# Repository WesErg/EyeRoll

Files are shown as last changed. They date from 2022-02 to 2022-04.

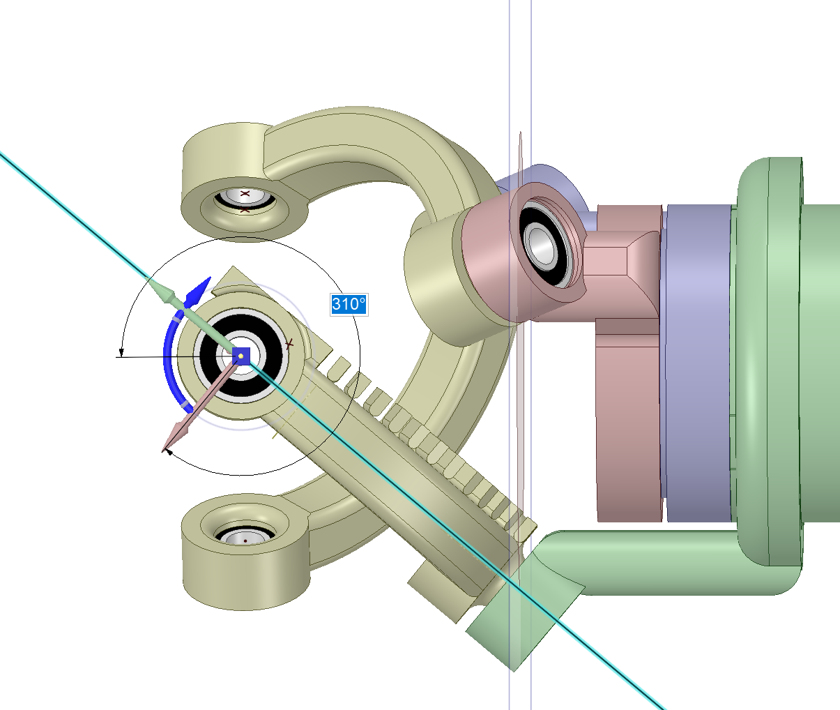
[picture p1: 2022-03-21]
doc/photos/Measure_joint_3_2_orientation.png

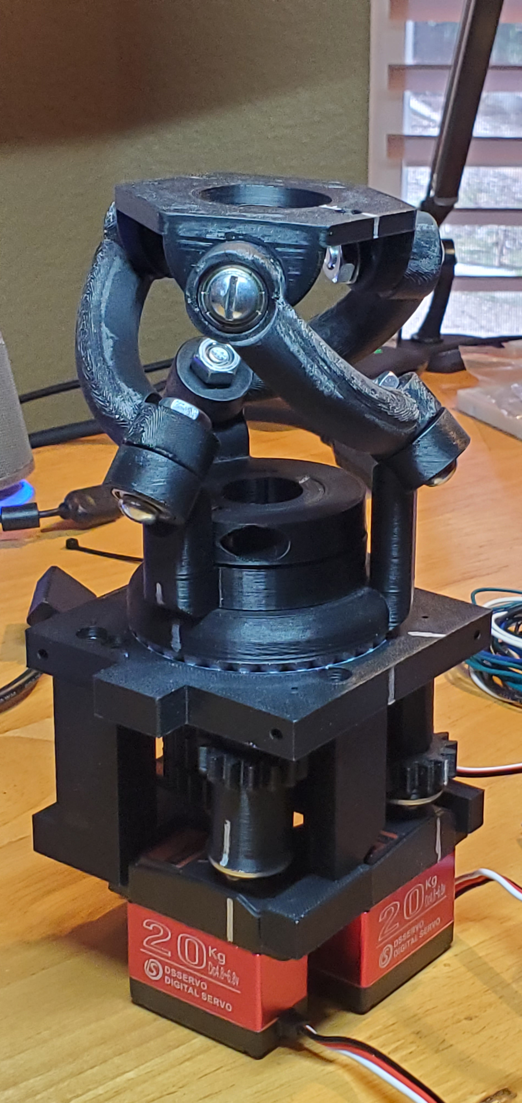
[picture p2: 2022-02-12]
doc/photos/wrist_assembled.jpg

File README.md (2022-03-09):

# EyeRoll
Project Eye Roll captures my explorations with a parallel spherical joint wrist (neck) as a means to produce a human eye roll.

A funny story ... never mind.

## References

[DruppThingaVerse](https://www.thingiverse.com/thing:2059967/files) Inmoov_New Neck by Drupp January 24, 2017.

[DruppInmoov](https://www.drupp.eu/inmoov.html) Drupp's inmoov page.

[Bulgarelli, et. al.](https://journals.sagepub.com/doi/pdf/10.5772/64113) A Low-cost Open Source 3D-Printable Dexterous Anthropomorphic Robotic Hand with a Parallel Spherical Joint Wrist for Sign Languages Reproduction.

[Sudki, Lauria, Nuca](https://www.marinepropulsors.com/proceedings/2013/10A.3.pdf) Marine Propulsor based on a Three-Degreee-of-Freedom Actuated Spherical Joint

[VideoServoTest](https://youtu.be/cDstRL1lU_U) video excercising joint

[Be Quiet](https://odriverobotics.com/#odrive)

## Project Manafest (fancy to do list right now)
- [ ] Jupyter notebook capturing the math
- [ ] Bill of Materials
- [ ] Python joint driver

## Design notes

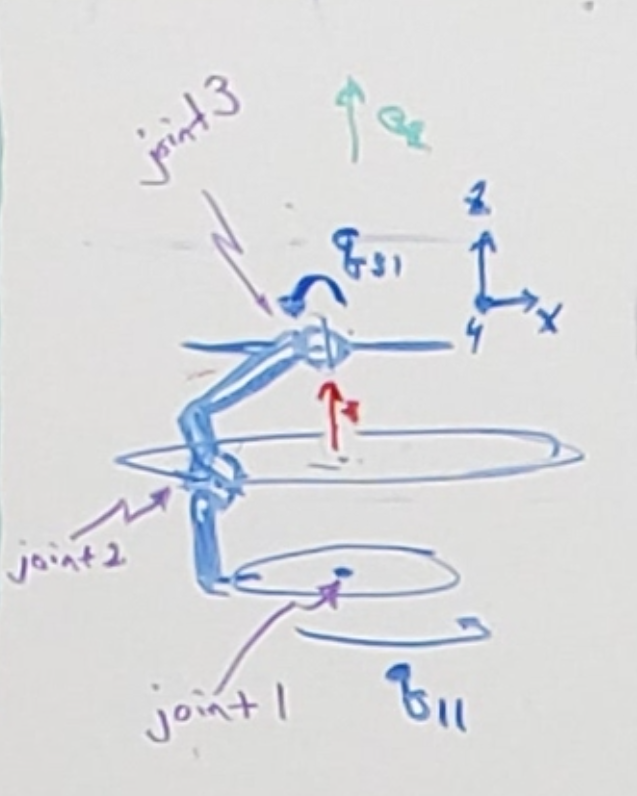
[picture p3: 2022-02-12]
doc/photos/wrist_joint_schematic.png

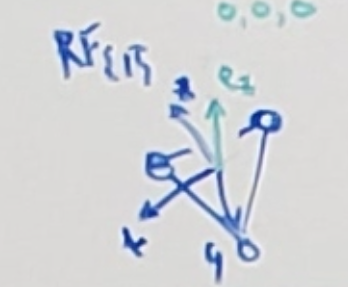
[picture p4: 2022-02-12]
doc/photos/wrist_rf_1_with_ez.png

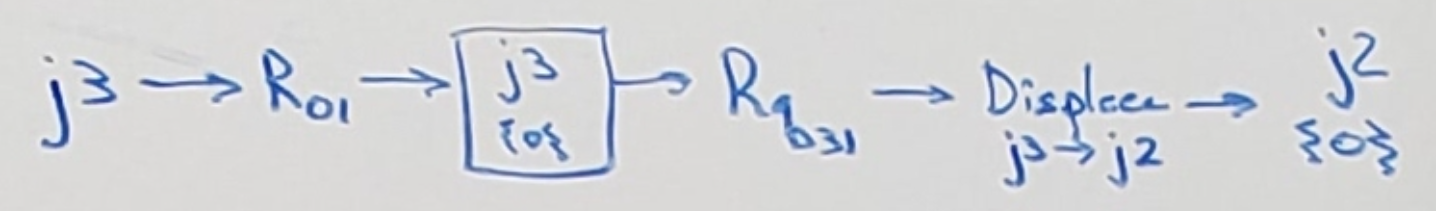
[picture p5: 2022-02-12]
doc/photos/wrist_joint_3_to_joint_2_chain.png

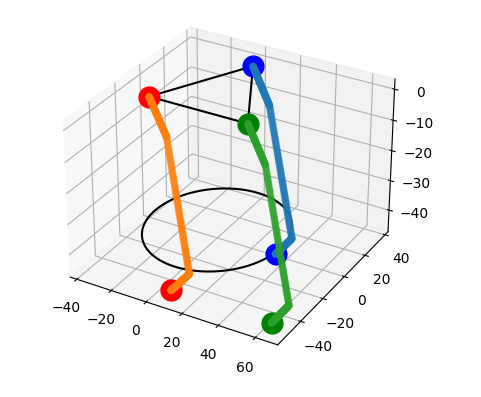
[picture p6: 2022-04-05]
doc/photos/blooper/eyeroll_blooper_3d_plot_1.png

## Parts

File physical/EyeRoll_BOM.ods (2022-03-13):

Qty. | Part Number | Size | Description | Use | Link
6 | B07FVXHWQR | 6 mm x 15 mm x 5 mm | Uxcell Carbon Steel Bearings | Neck arms | https://amazon.com/B07FVXHWQR /
32 | B07YKQ43B3 | 6 mm | Uxcell 304 Stainless Precision Bearing Balls | Neck green ring | https://amazon.com/B07YKQ43B3 /
6 | 92131A520 | 15 mm ID, .94 mm tall | Single Turn Spiral Internal Retaining Ring | Neck arm snap rings | https://mcmaster.com/92131A520/
6 | 90327A138 | M6 x 1, 20 mm | Alloy Steel Low-Profile Socket Head Screws | Neck arm lock nuts | https://mcmaster.com/90327A138/
6 | 90576A115 | M6 x 1, 6 mm | Medium Strength Steel Nylon Locknut | Neck arm bolts | https://mcmaster.com/90576A115/
1 | 91290A120 | M3 x .5, 16 mm | Black-Oxide Alloy Steel Socket Head Screw | Neck gear red bolt | https://mcmaster.com/91290A120/
1 | 97259A101 | M3 x .5, 1.8 mm | Low-strength Steel Thin Square Nut | Neck gear red nut | https://mcmaster.com/97259A101/
5 | 97259A101 | M3 x .5, 1.8 mm | Low-strength Steel Thin Square Nut | Neck drive plate nuts | https://mcmaster.com/97259A101/
5 | 91290A572 | M3 x .5, 15 mm | Black-Oxide Alloy Steel Socket Head Screw | Neck drive plate bolts | https://mcmaster.com/91290A572/
3 | 98381A507 | 3/16” OD, 5/8” long | Dowel Pin | Neck drive pinion rod | https://mcmaster.com/98381A507/
3 | 6391K114 | 3/16” ID, 5/16” OD, ¼” long | Oil-Embedded Bronze Sleeve Bearing | Neck drive pinion bushing | https://mcmaster.com/6391K114/
12 | 97259A101 | M3 x .5, 1.8 mm | Low-strength Steel Thin Square Nut | Neck drive servo nuts | https://mcmaster.com/97259A101/
12 | 91294A132 | M3 x .5, 12 mm | Black-Oxide Hex Drive Flat Head Screw | Neck drive servo bolts | https://mcmaster.com/91294A132/
3 | B076CNKQX4 |  | DS3218 ANNIMOS 20KG 270 High Torque Servo | Neck drive | https://amazon.com/B076CNKQX4/
3 | B07NS5PLHV | 25T | Uxcell Servo Arm Horn Aluminum 25T | Neck drive | https://amazon.com/B07NS5PLHV/

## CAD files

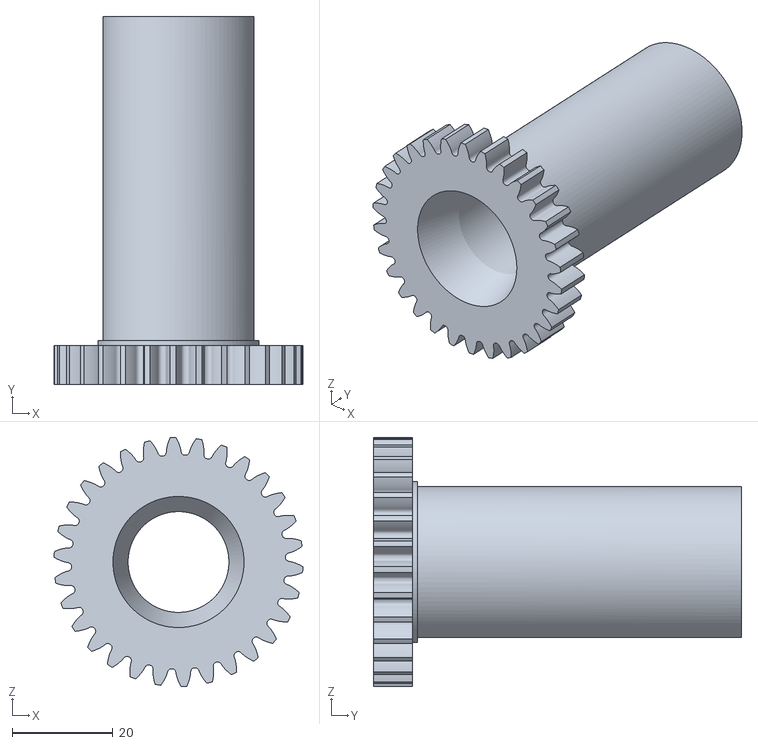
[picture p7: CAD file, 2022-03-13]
physical/STL/Gear_red.stl
49.4 x 73.0 x 49.4

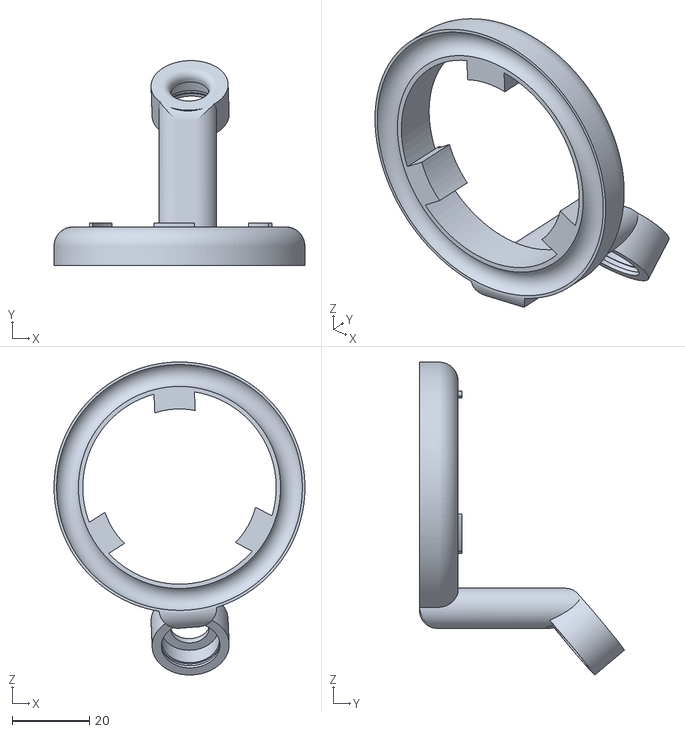
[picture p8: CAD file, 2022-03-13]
physical/STL/Ring_green.stl
65.0 x 53.0 x 81.1

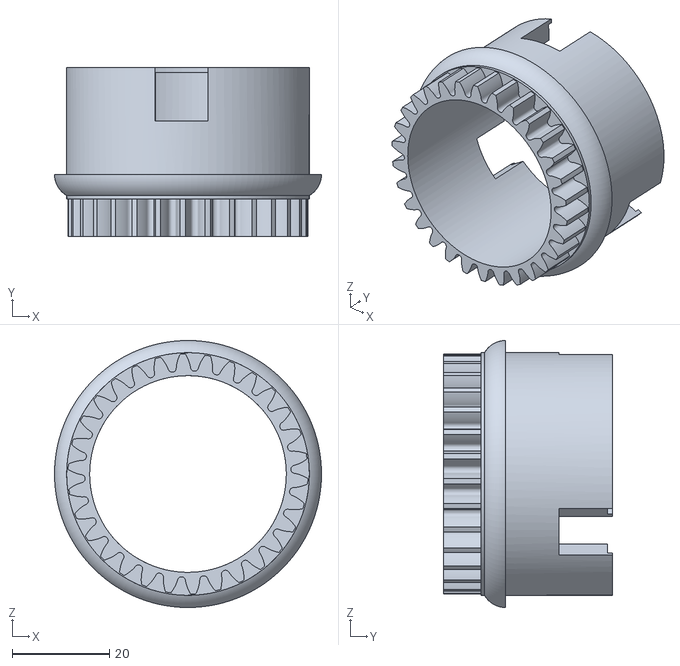
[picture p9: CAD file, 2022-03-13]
physical/STL/Gear_green.stl
55.0 x 34.7 x 55.0

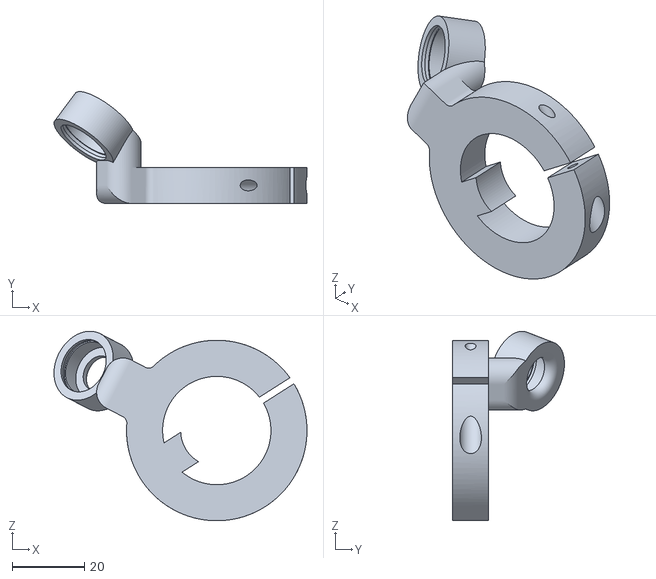
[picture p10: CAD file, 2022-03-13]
physical/STL/Ring_red.stl
70.1 x 31.0 x 52.5

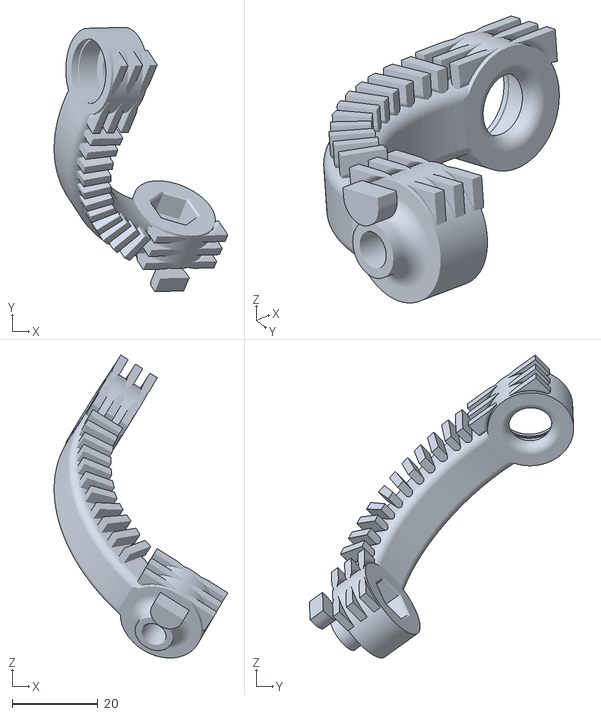
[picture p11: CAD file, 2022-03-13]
physical/STL/Arm_with_support.stl
40.5 x 61.6 x 70.6

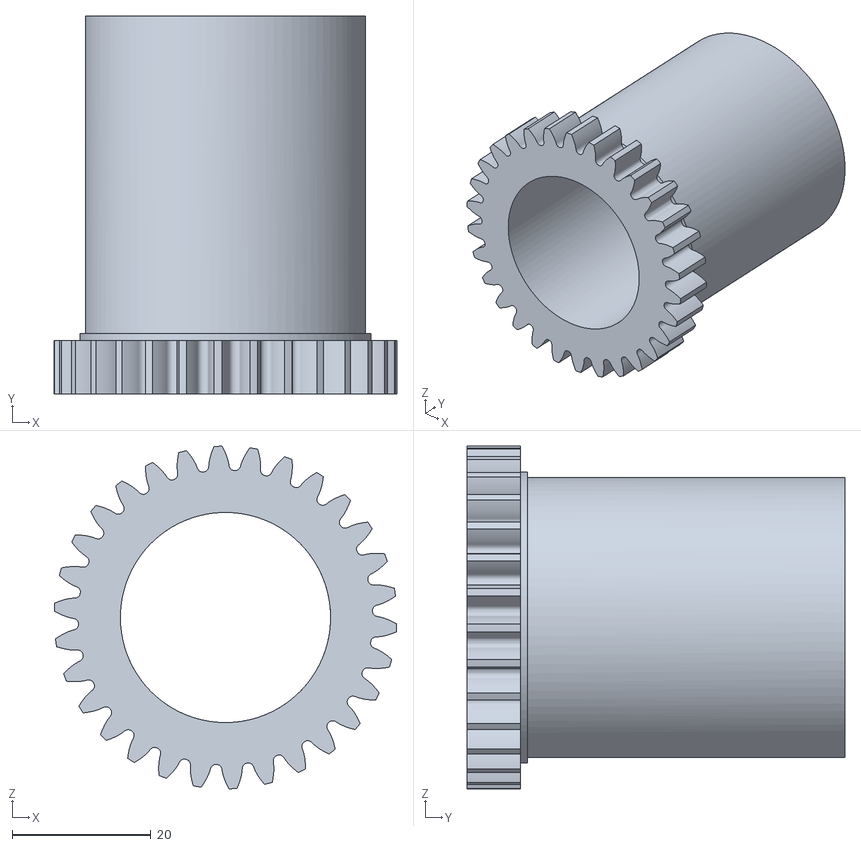
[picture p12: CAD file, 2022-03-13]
physical/STL/Gear_blue.stl
49.4 x 54.5 x 49.4

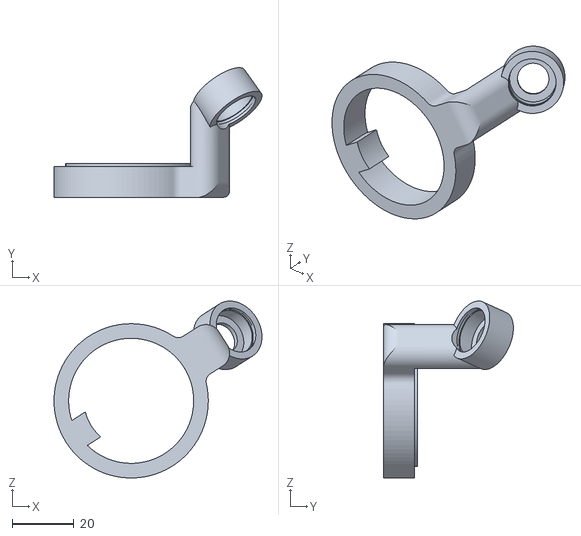
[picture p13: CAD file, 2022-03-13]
physical/STL/Ring_blue.stl
67.4 x 42.1 x 57.3

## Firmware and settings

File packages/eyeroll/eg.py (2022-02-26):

from eyeroll.gpio.pwm_generate import WesPWM
import pigpio
import time

def exercise_1(sn, N=100, dt=0.03):
    sn.goto(-1)
    time.sleep(.15)
    for n in range(N):
        sn.goto(-1 + 2 * float(n) / N)
        time.sleep(dt)
    time.sleep(.15)
    sn.zero()

def n_sign(n):
    return [1., -1][n%2]

def exercise_2(sns, N=100, dt=0.03):
    for n, sn in enumerate(sns):
        sn.goto(.5*n_sign(n))
    time.sleep(.15)
    for n in range(N):
        for nn, sn in enumerate(sns):
            sn.goto(n_sign(nn)*(.5 - float(n) / N))
        time.sleep(dt)
    for n in range(N):
        for nn, sn in enumerate(sns):
            sn.goto(-n_sign(nn)*(.5 - float(n) / N))
        time.sleep(dt)
    time.sleep(.15)
    for sn in sns:
        sn.zero()


if __name__ == "__main__":
    pi = pigpio.pi()
    s1 = WesPWM(pi, 5, double_range=True)
    s2 = WesPWM(pi, 6, double_range=True)
    s3 = WesPWM(pi, 26, double_range=True)

    s1.zero(); s2.zero(); s3.zero()
    time.sleep(.5)

    exercise_1(s1)
    exercise_1(s2)
    exercise_1(s3)
    exercise_2([s1, s2, s3])
    s1.zero(); s2.zero(); s3.zero()
    time.sleep(.5)

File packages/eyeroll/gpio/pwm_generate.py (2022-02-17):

import pigpio


class WesPWM:
    HW_PWM = 1
    SW_PWM = 0

    def __init__(self, pi, gpio, frequency=100, double_range=True):
        self.pi = pi
        self.gpio = gpio

        self.pi.set_mode(gpio, pigpio.OUTPUT)
        self.frequency = frequency
        self.duty = None
        self.position = 0.

        self._double_range = double_range

        if False and gpio in {12, 13, 18, 19}:  # "HW PWM only supported gpio pins: 12, 13, 18, 19"
            self.type = self.HW_PWM
            self._init_hw_pwm()
        else:
            self.type = self.SW_PWM
            self._init_sw_pwm()

    def _init_hw_pwm(self):
        self.full_range = 1000000
        self.zero_duty = int( (3 * 1000000) / (2*20) )  # 1M = 20 msec
        self.half_range = int(self.zero_duty / 3)
        if self._double_range:
            self.half_range *= 2
        self.duty = self.zero_duty
        self.goto(0)

    def _init_sw_pwm(self):
        # default sample rate is 5 us yielding possible PWM frequencies of:
        #  8000 4000 2000 1600 1000 ... 50 40 20 10 ... 20 is what we want.
        #  http://abyz.me.uk/rpi/pigpio/python.html#set_PWM_frequency
        self.full_range = 10000  # max range resolution is 40000
        self.zero_duty = 1500
        self.half_range = 500
        if self._double_range:
            self.half_range *= 2
        self.duty = self.zero_duty
        self.pi.set_PWM_frequency(self.gpio, self.frequency)
        self.pi.set_PWM_range(self.gpio, self.full_range)
        self.pi.set_PWM_dutycycle(self.gpio, self.zero_duty)

    def zero(self):
        self.goto(0)

    def goto(self, value):
        """
        Set the value of the servo duty cycle
        :param value: -1 to +1
        :return:
        """
        self.duty = int(value * self.half_range) + self.zero_duty
        if self.type == self.HW_PWM:
            self.pi.hardware_PWM(self.gpio, self.frequency, self.duty)
        else:
            self.pi.set_PWM_dutycycle(self.gpio, self.duty)

        self.position = value
        return self.position

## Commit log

2022-02-12 added Joint angle derivation as jupyter notebook.
2022-02-17 Added PWM control using pigppio and pigipiod
2022-03-13 Added Physical
    [Arm_with_support.stl, EyeRoll_BOM.ods, Gear_blue.stl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]
